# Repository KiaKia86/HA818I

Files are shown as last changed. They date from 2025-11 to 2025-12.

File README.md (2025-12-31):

# *HA818I*

### A high-performance custom rocket designed entirely from scratch, using a 4-layer avionics PCB, custom airframe, and custom solid motor. The rocket is expected to reach **12,000 ft (≈3657.6 m)** at **Mach 0.6**, powered by a **385 N thrust** motor.

### The airframe is constructed with lightweight composite sections reinforced with fiberglass cloth and resin. The rocket includes 2 pyro channels, offering flexibility for multiple deployments and different control configurations.

### The avionics is built on a 4-layer PCB with one microcontroller (ESP32-S3) working to process flight data and transmit telemetry via LoRa to the ground station. The board includes multiple sensors to track acceleration, rotation, altitude, and GPS position.



---

# Bill of Materials (BOM) (FOR Hack Club!!!)

| **Category** | **Item** | **Est. Price**  | **Purchase Link** |
|---|---|---|---|
| Structure | Fiberglass Cloth (6oz) | $21.99  | https://www.amazon.com/Fiberglass-Fabric-Glass-Repair-Surfboard/dp/B0DN5FFPSV |
| Structure | Fiberglass Cloth (4oz) | $42.99 | https://www.amazon.com/YIQUEDOK-Fiberglass-48-75-Sq-Ft-Surfboard-Repair/dp/B0F74917P7 |
| Structure | Econostitch Peel (5 yards) | $29.95  | https://www.amazon.com/Fibre-Glast-Econostitch-Package-Visible/dp/B07DP3PNPJ |
| Structure | TotalBoat 5:1 Marine Epoxy | $68.99 | https://www.amazon.com/TotalBoat-Epoxy-Quart-Fast-Hardener/dp/B00HR85152 |
| Structure | Primer | $7.97 | https://www.amazon.com/Rust-Oleum-Automotive-260510-12-Ounce-Sandable/dp/B006ZLQ4HQ |
| Structure | Paint | $6.19 | https://www.amazon.com/Rust-Oleum-249127-Painters-Purpose-12-Ounce/dp/B002BWOS7Q |
| Structure | Plastic Drop Cloth | $9.47  | https://www.amazon.com/Plastic-Drop-Cloths-6-Pack-Disposable/dp/B0DQDWV1SV |
| Recovery | Parachute (36 inch) | $18.69 | https://www.apogeerockets.com/Building-Supplies/Parachutes/Larger-than-24in/36in-Printed-Nylon-Parachute/Review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 |
| Recovery | Kevlar Shock Cord | $40.69  | https://www.apogeerockets.com/Building-Supplies/Shock-Cord/Kevlar-Shock-Cord-4500-20-feet-long-3-loops |
| Structure | Bulkheads | $41.24  | N/A Custom Quote (Merchandise fee is waived, only shipping cost)  |
| Avionics | PCBA Shipping Cost | $42.22 | N/A Custom Quote (Merchandise fee is waived, only shipping cost) |
| Avionics | 433Mhz Antenna | $9.99  | https://www.amazon.com/dp/B0FB3MDJG1?ref=ppx_yo2ov_dt_b_fed_asin_title&th=1 |
| Avionics | High Gain GPS Antenna | $12.79  | https://www.amazon.com/dp/B0B2NGKCY1?ref=ppx_yo2ov_dt_b_fed_asin_title |
| Avionics | 2.4Ghz Antenna | $8.99 | https://www.amazon.com/dp/B099R3GR91/?th=1 |

**Total Estimated Cost: $362.16**

**Note:**
The PCB cost is not included in the bom, as it is funded by an external source (JLCPCB). Filament and other materials on hand are not considered either!

---

### PCB Overview

The **4-layer PCB** serves as the core of the HA818I flight computer.  
It uses:
- **ESP32-S3** (Telemetry, communication, logging, and sensor data)  
- **LoRa radio module** for long-range ground communication  
- Multiple onboard sensors: **IMU**, **barometer**, **magnetometer**, **GPS**, and **accelerometer**  
- **Two pyro channels** for deployment   

The avionics system is designed for flexibility, allowing reuse across future rocket designs.




---

### Why Did I Make This Rocket?

I've wanted to design something that combines all of my passions into one project, and this is it. HA818I represents months of hard work, simulation, and testing. Everything I learned about propulsion, control, and flight dynamics has been combined into a single rocket! 

---

# Physical Build
Pictures are being edited!

# Sponsors

<div align="center">

## Proudly Sponsored By

<table>
  <tr>
    <td align="center" width="50%">
      <a href="https://jlcpcb.com" target="_blank">
        JLCPCB
      </a>
    </td>
    <td align="center" width="50%">
      <a href="https://oshwlab.com/explore" target="_blank" rel="noopener noreferrer">
        OSHWLab
      </a>
    </td>
  </tr>
</table>

This project is made possible by the generous support of **JLCPCB** and **OSHWLab**. Their commitment to the open hardware community and maker ecosystem enables innovative projects like this to come to life.

</div>

---

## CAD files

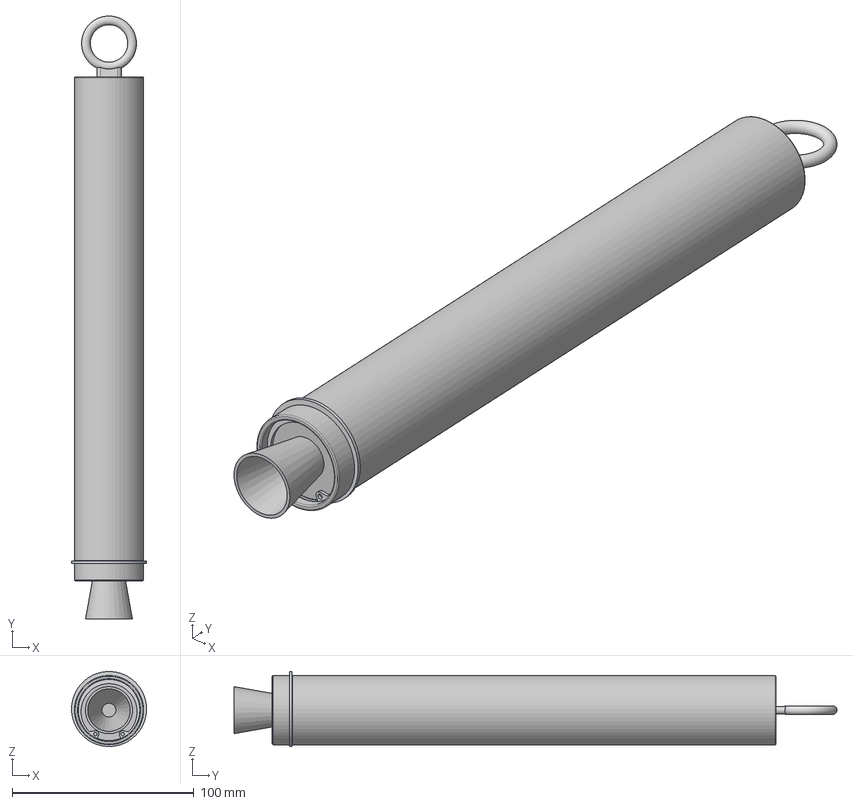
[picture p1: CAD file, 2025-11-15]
CAD/Motor/STEP/Motor (Assembled)_.step
41.3 x 331.7 x 41.3 mm
Tube
Nozzle
Forward Closure
O-Ring (9452K35) x 2
Retaining Ring (98409A232) x 2
Spiral Retaining Ring (91650A510)
Eyebolt (3014T45)
38mm Tube Liner
Propellant With Case (2.25 H/0.5 ID/1.212 OD) x 4

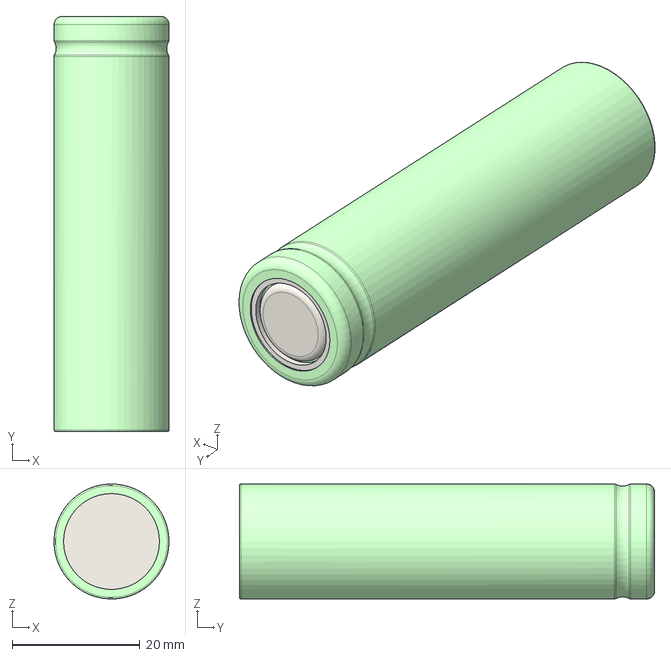
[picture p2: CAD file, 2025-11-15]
CAD/Electronics/STEP/Generic Li Ion 1850 cell_.step
18.0 x 65.0 x 18.0 mm

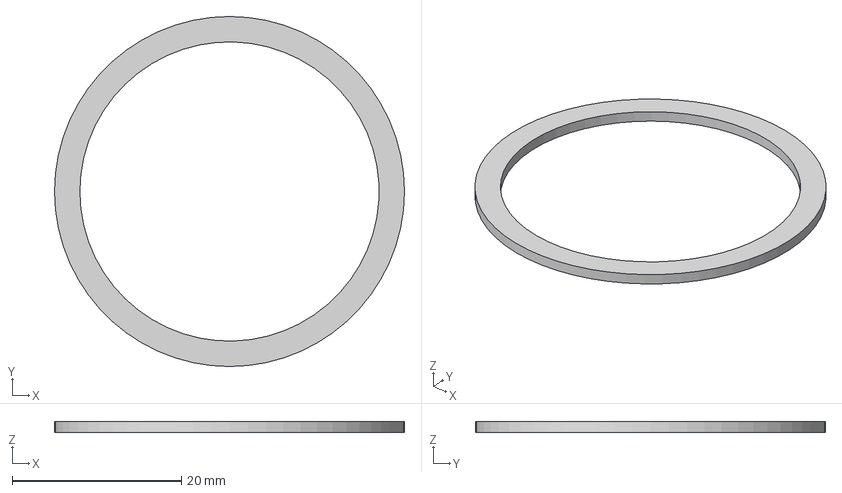
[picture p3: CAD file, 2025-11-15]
CAD/Motor/STEP/Spiral Retaining Ring (91650A510).step
41.3 x 41.3 x 1.27 mm

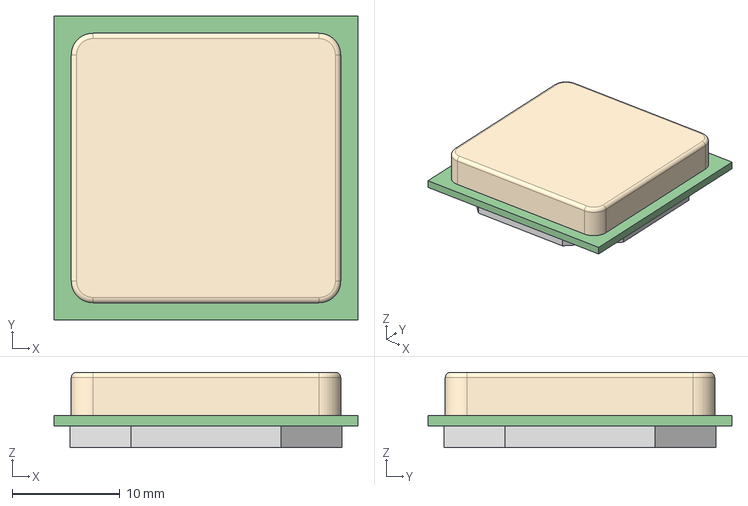
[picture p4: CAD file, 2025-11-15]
CAD/Electronics/STEP/GPS.step
28.2 x 28.2 x 7.00 mm

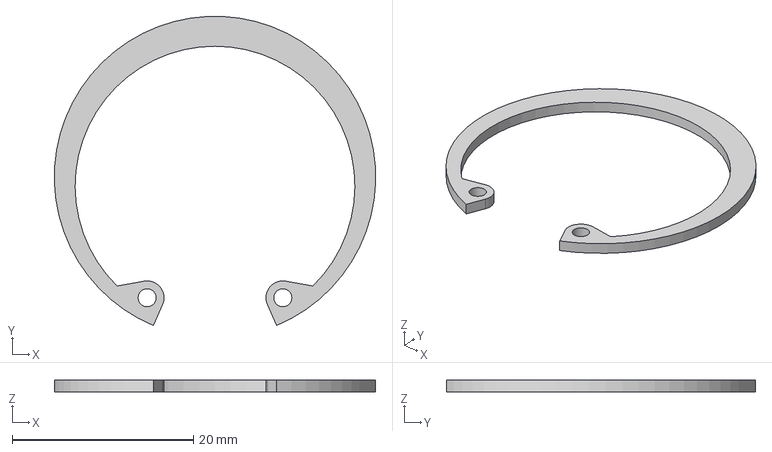
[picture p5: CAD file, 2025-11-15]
CAD/Motor/STEP/Retaining Ring (98409A232).step
35.4 x 34.1 x 1.27 mm

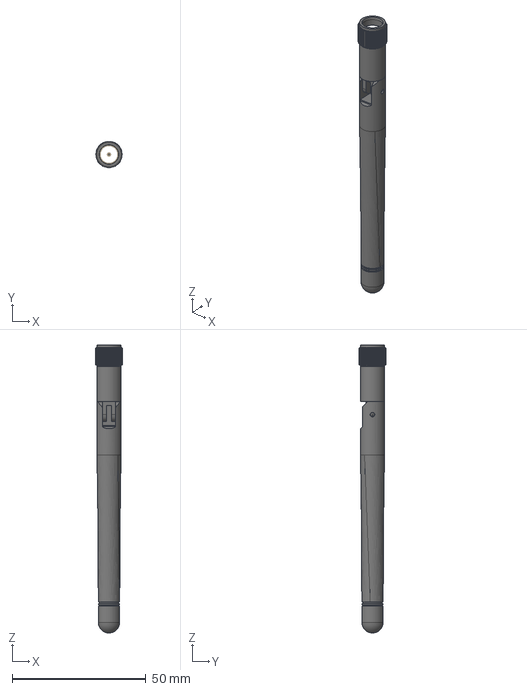
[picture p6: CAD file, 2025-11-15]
CAD/Electronics/STEP/Antenna.step
10.00 x 9.99 x 107.5 mm
2.4 GHz Antenna Base
2.4 GHz Antenna Top

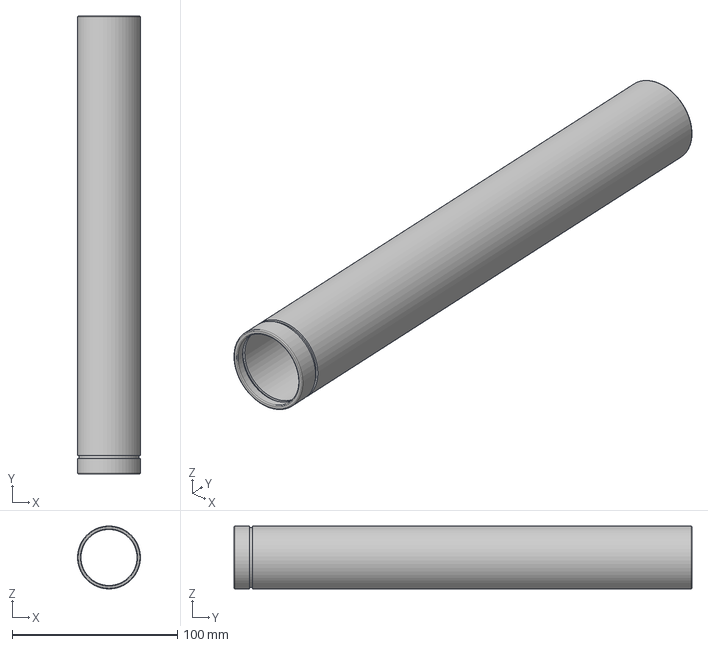
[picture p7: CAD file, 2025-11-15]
CAD/Motor/STEP/Tube.step
38.1 x 277.2 x 38.1 mm

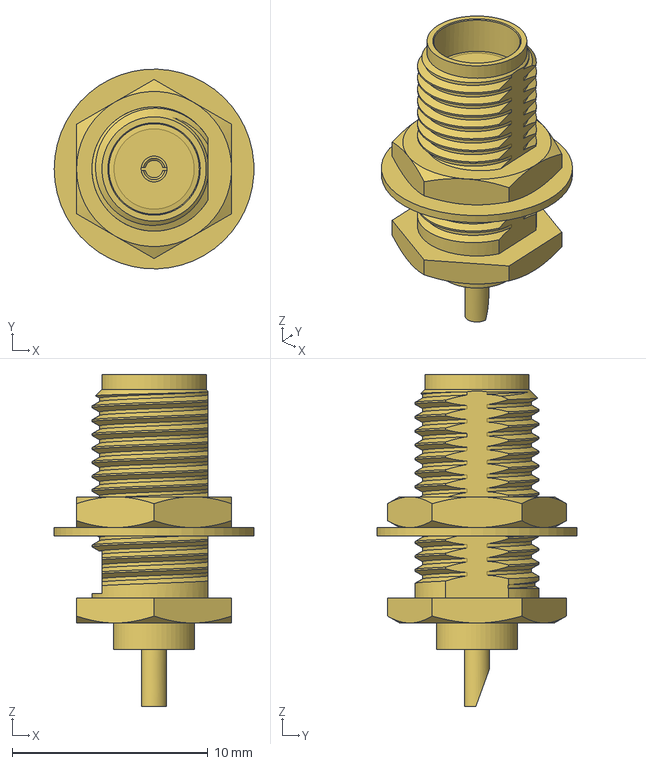
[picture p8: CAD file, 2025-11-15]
CAD/Electronics/STEP/RF Connector.step
10.2 x 10.2 x 17.0 mm

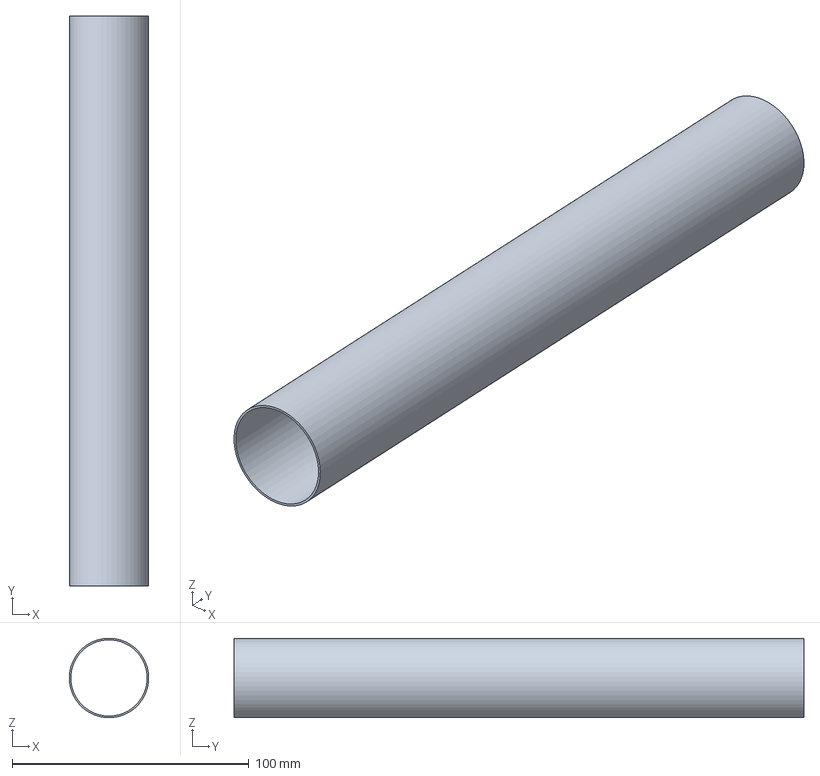
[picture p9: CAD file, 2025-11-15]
CAD/Motor/STEP/38mm Tube Liner_.step
33.6 x 241.0 x 33.6 mm

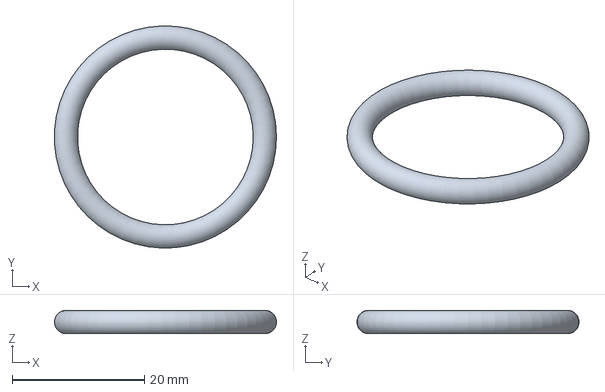
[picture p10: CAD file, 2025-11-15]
CAD/Motor/STEP/O-Ring (9452K35)_.step
33.6 x 33.6 x 3.53 mm

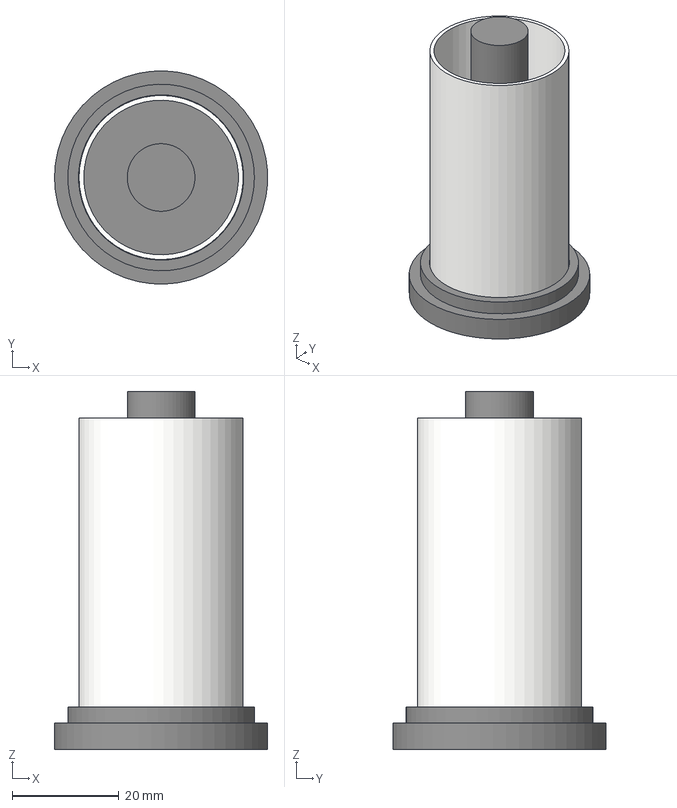
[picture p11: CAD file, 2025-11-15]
CAD/Motor/STEP/GrainCasing.step
40.0 x 40.0 x 67.2 mm

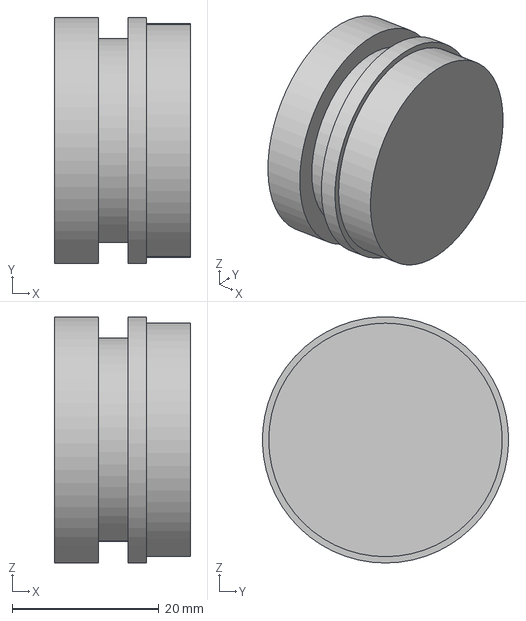
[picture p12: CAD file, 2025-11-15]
CAD/Motor/STEP/Forward Closure_.step
18.5 x 33.5 x 33.5 mm

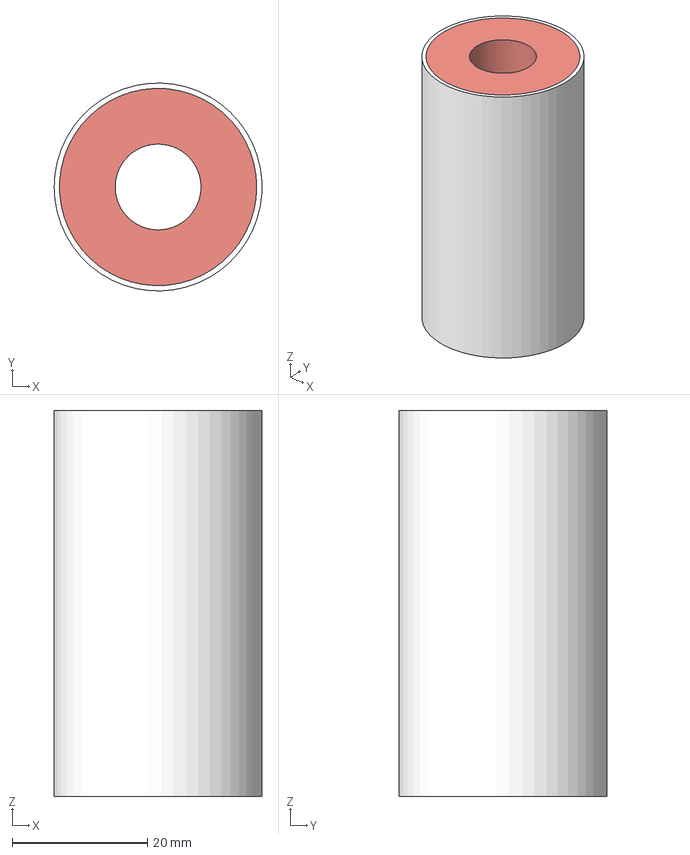
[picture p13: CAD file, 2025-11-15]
CAD/Motor/STEP/Propellant With Case.step
30.8 x 30.8 x 57.1 mm

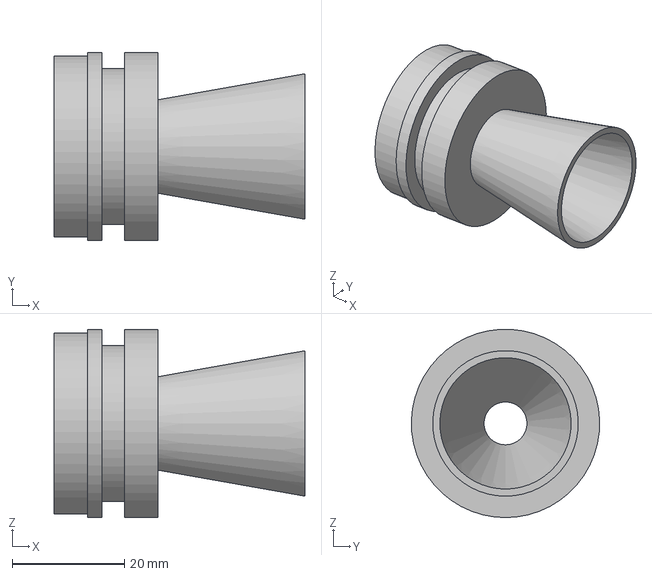
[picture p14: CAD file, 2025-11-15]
CAD/Motor/STEP/Nozzle_.step
44.7 x 33.5 x 33.5 mm

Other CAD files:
CAD/Motor/STEP/Eyebolt (3014T45)_.step
CAD/Electronics/STL/Antenna.stl
CAD/Electronics/STL/GPS.stl
CAD/Electronics/STL/Generic Li Ion 1850 cell_.stl
CAD/Electronics/STL/RF Connector.stl
CAD/Motor/STL/38mm Tube Liner_.stl
CAD/Motor/STL/Eyebolt (3014T45)_.stl
CAD/Motor/STL/Forward Closure_.stl
CAD/Motor/STL/GrainCasing.stl
CAD/Motor/STL/Motor (Assembled)_.stl
CAD/Motor/STL/Nozzle_.stl
CAD/Motor/STL/O-Ring (9452K35)_.stl
CAD/Motor/STL/Propellant With Case.stl
CAD/Motor/STL/Retaining Ring (98409A232).stl
CAD/Motor/STL/Spiral Retaining Ring (91650A510).stl
CAD/Motor/STL/Tube.stl

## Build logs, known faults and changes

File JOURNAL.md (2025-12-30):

| Title | Author | Description | Created_at |
|---|---|---|---|
| HA818I | Kiya | A high-performance custom rocket with full avionics, airframe, and motor designed from scratch. | 2025-10-02 |

# Dev Log "HA818I"

**Total Time (Hours): 42 Hours**

---

## Week 1 (10/02/2025) – 8 Hours  

**Days worked on:**  
Thursday – 2 hours<br>
Friday – 1 hour<br>
Saturday – 3 hours<br>
Sunday – 2 hours  

- Started to plan the rocket
- Created an open rocket simulation to predict how fast the rocket would go
- Made sketches and a model (Very rough) to get an idea of what the rocket would look like 
- Researched materials for motor (304 steel and 6061 aluminum)
- Modeled nose cone and body tube in Fusion 360

**Open Rocket Simulation**

**Body Tube**

**Nose Cone**


---

## Week 2 (10/09/2025) – 10 Hours  

**Days worked on:**  
Monday – 2 hours<br>
Tuesday – 2 hours<br>
Wednesday – 3 hours<br>
Thursday – 2 hours<br>
Friday – 1 hour  

- Designed the finalized the motor size (38mm x 277mm, with 385N of thrust) 
- Modeled grain holders  
- Started designing 4-layer avionics PCB  
- Designed fins based on the openrocket simulation and data  
- Confirmed center of gravity and stability margin through simulations

**Full Motor Design**

**Motor Cross Section**

**Propellant Case Mold**

**Fins**


---

## Week 3 (10/16/2025) – 9 Hours  

**Days worked on:**  
Monday – 2 hours<br>
Tuesday – 1 hour<br>
Wednesday – 3 hours<br>
Thursday – 2 hours<br>
Friday – 1 hour  

- Started and finished the schematic for the flight controller
- Added two pyro channels for deployment
- Designed the bulkheads of the rocket
- Started PCB layout using the SGGS rule (EMI protection)
  
**PCB schematic**

**Motor retainers and bulkheads**

**Pyro Channels**


---

## Week 4 (10/23/2025) – 8 Hours  

**Days worked on:**  
Monday – 1 hour<br>
Tuesday – 2 hours<br>
Wednesday – 2 hours<br>
Thursday – 1 hour<br>
Friday – 2 hours  

- Finished the PCB layout with optimization
- Double-checked all wiring
- Checked design rule, and everything looked good
- Started to download libraries in preparation for the PCBs

**PCB Layout**


---

## Week 5 (10/30/2025) – 7 Hours  

**Days worked on:**  
Monday – 1 hour<br>
Tuesday – 2 hours<br>
Wednesday – 1 hour<br>
Thursday – 2 hours<br>
Friday – 1 hour  

- Designed avionics enclosure
- Added 2s battery support
- Researched composites and practiced with friends
- Researched things needed for recovery
- Optimized BOM 

**Avionics Bay**


## Full Rocket Image!


---

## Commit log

2025-11-12 Create Motor
2025-11-12 Create CAD
